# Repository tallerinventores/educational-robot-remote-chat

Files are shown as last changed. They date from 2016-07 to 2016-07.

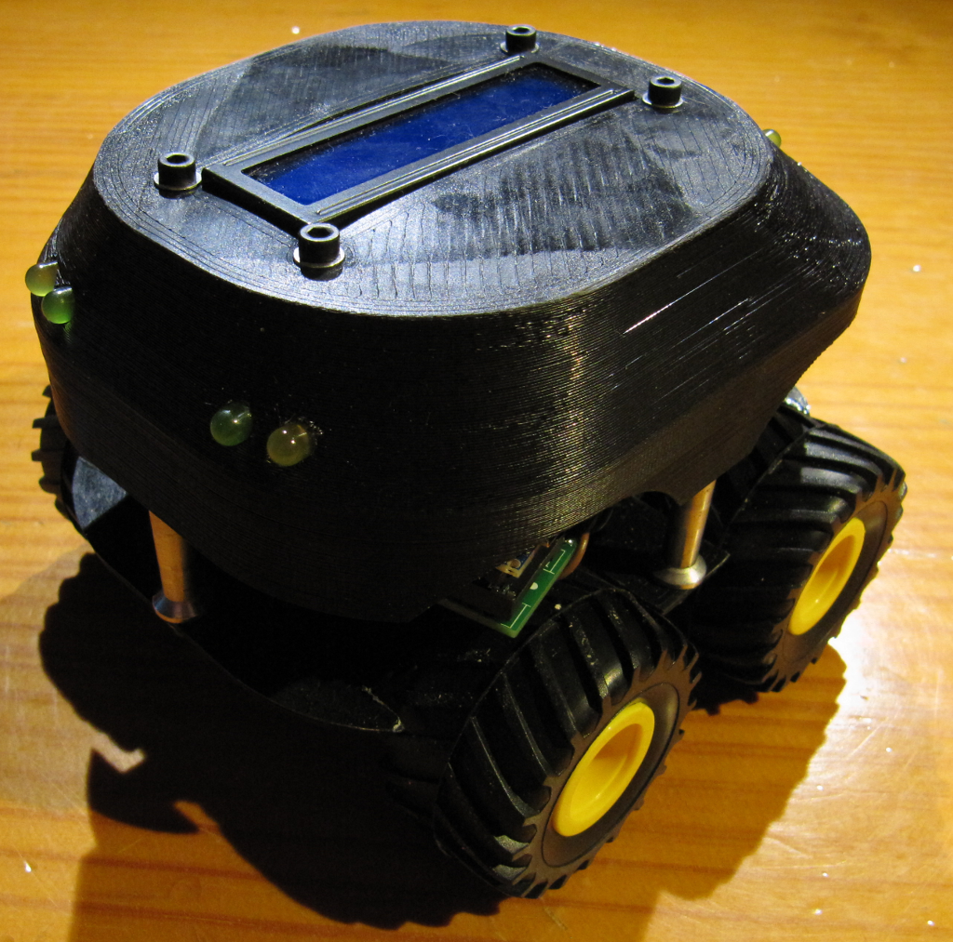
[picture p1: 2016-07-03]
img/photo-errc-2.png

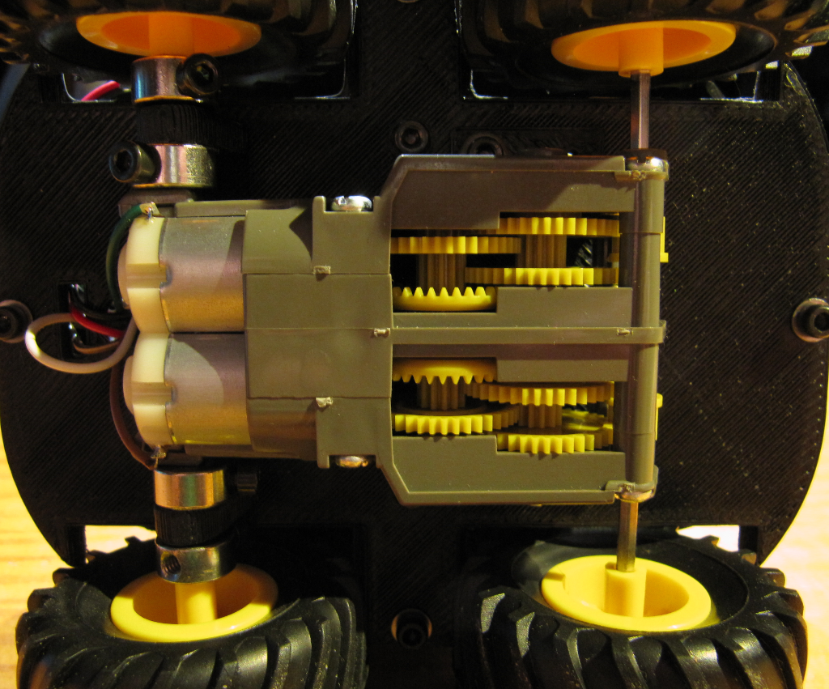
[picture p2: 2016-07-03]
img/photo-errc-5.png

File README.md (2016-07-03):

# educational-robot-remote-chat #

> RC robot w/ chat capabilies for educational use  

* * *

## Resumen ##

Robot interactivo diseñado por los alumnos de la actividad de robótica [Taller
de Inventores](http://tallerinventores.github.io/). Ha sido desarrollado y
optimizado para impresión 3D y pensando en su bajo coste y facilidad de montaje
y uso.

## Instalación ##

En esta sección se cubre la instalación de software y hardware para el montaje
recomendado, mediante [Arduino](http://www.arduino.cc/).

### Requerimientos de software ###

Para poser usar Arduino (v1.6+) con el código fuente proporcionado, son
necesarias las librerías [NewPing](http://playground.arduino.cc/Code/NewPing) y
[NewLiquidCrystal](https://bitbucket.org/fmalpartida/new-liquidcrystal/downloads).
Para generar los archivos aptos para la impresora 3D desde los archivos `.stl`
será necesario adicionalmente un software para esta función, como puede ser
[Slic3r](http://slic3r.org/).

### Requerimientos de hardware ###

Será necesario para su montaje y uso cuatro pilas tipo AA, una pantalla LCD de
dieciséis por dos con interfaz I2C, un sensor de distancia por ultrasonidos tipo
HC-SR04, seis LED de colores, seis resistencias de 330Ω, una de 2,7kΩ, un
transistor BC547, un conjunto de motor Tamiya Twin-Motor y cuatro ruedas Tamiya
Off-road, una placa Robgednaut Zond con un Arduino Nano o compatible y un módulo
de bluetooth HC05. Adicionalmente harán falta tornillos y arandelas de métrica
tres. Se recomienda un macho de misma métrica.

## Uso ##

Instrucciones de montaje y puesta en marcha.

### Montaje del robot ###

1.  Imprimir una unidad de los archivos `chassis.stl` y `base.stl`. Imprimir
    cuatro unidades de `spacer.stl`. Puede ser necesario repasar las piezas
    impresas con el fin de eliminar rebabas.  
2.  Montar la pantalla LCD sobre la parte superior del robot (_chassis_) usando
    cuatro tornillos de métrica tres por doce con arandela, insertados de la
    parte plástica hacia la pantalla, y asegurados con una tuerca cada uno.  
3.  Montar los LED en sus orificios y fijarlos con plástico termofusible si
    fuera necesario.  
4.  Montar el sensor de distancia en el frontal del chasis.  
5.  Presentar el portapilas sobre la parte interior de la parte inferior del
    robot (_base_) y alinear los agujeros de fijación, usar dos tornillos de
    métrica tres por seis, roscando sobre el la estructura del portapilas.  
6.  Montar el motor en la parte externa de la base, y fijarlo mediante dos
    tornillos de métrica tres por seis sobre la rosca que se realiza en sus
    agujeros correspondientes, de forma que quede alineado el eje motriz con el
    centro del hueco de las ruedas.  
7.  Realizar la gestión de cables del motor y del sensor de distancia para que
    entren al cuerpo del robot a través del agujero destinado a ello.  
8.  Montar las ruedas traseras en los ejes del motor.  
9.  Posicionar los ejes delanteros en los agujeros de la base, y montar un
    anillo de retención a cada extremo con tornillos de métrica tres por seis.
    Colocar las ruedas delanteras.  
10. Realizar todas las uniones eléctricas.  
11. Cerrar el robot con tornillos de métrica tres por treinta con arandela,
    añadiendo un espaciador (_spacer_) en cada tornillo entre ambas partes
    principales del robot. Roscar dichos tornillos sobre la rosca previamente
    hecha en los orificios para este propósito de la mitad superior.

### Conexión eléctrica ###

Este proyecto usa [Robgednaut](http://akornsys-rdi.github.io/robgednaut/) Zond
como placa de conexionado, si no dispones de ella puedes ver su esquema de
conexiones en la página oficial.  

Las alimentaciones para todos los dispositivos las provee la placa de control.
Los cables de señal de la pantalla SDA y SCL están conectados a C y D
respectivamente. Las señales del sensor de distancia por ultrasonidos ECHO y
TRIGGER están conectadas a B y A respectivamente. Cada motor está conectado a un
canal de la salida para motores, respetando su polaridad.  

Los LED del robot llevan una resistencia de 330Ω en el ánodo, todos ellos
conectados entre sí y al pin de alimentación de la pantalla. Los cátodos van al
colector del transistor. El emisor está conectado a la masa de la pantalla, y la
base va conectada al pin del expansor I2C que controla la retroiluminación de la
pantalla LCD a través de una resistencia de 2,7kΩ.  

### Firmware ###

El Arduino deberá tener cargado el firmware de control que se incluye en la
carpeta `src` de este repositorio.  

### Software ###

Con la comunicación bluetooth establecida (elementos emparejados), abrir una
aplicación terminal en el dispositivo de control (por ejemplo cutecom) y 
escribir la frase o comando que se desee enviar, finalizada por el caracter
retorno de carro (`0x13`).  

### Bugs ###

Se han observado los siguientes problemas:  

-   Debido a todo el hardware que va dentro del robot, han sido necesarios
    añadir unos separadores entre el chasis y la base.  
-   El interruptor de encendido/apagado es difícil de accionar al quedar dentro
    de la estructura.  
-   Enviar palabras sueltas que no sean comandos, parecen no funcionar.  
-   El software de control provoca al inicio movimientos extraños.  

## Enlaces externos ##

Este proyecto también está presente en:  

-   [Thingiverse](http://www.thingiverse.com/thing:1656508).  

## Créditos ##

Proyecto realizado por Taller de Inventores 2016, representado por:  

-   kwendenarmo <kwendenarmo@akornsys-rdi.net>  

Alumnos del Centro de Formación Padre Piquer:  

-   G, Ayman El-  
-   S, Rubén  
-   S, Sergio

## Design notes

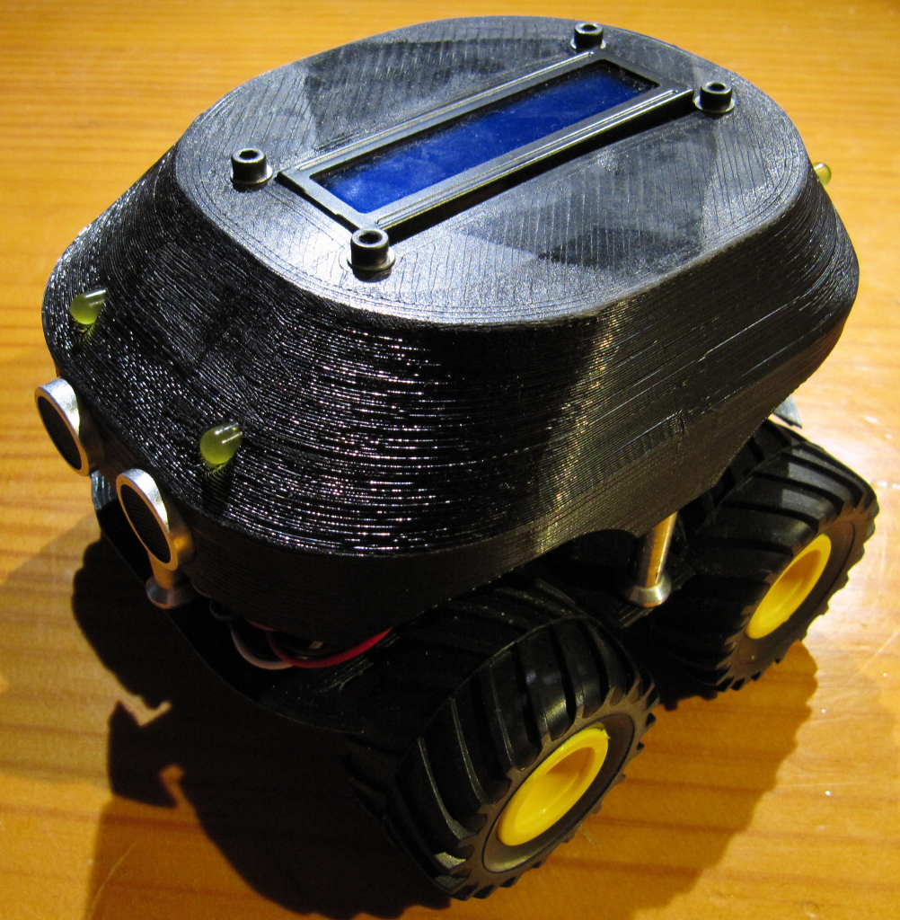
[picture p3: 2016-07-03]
img/photo-errc-1.png

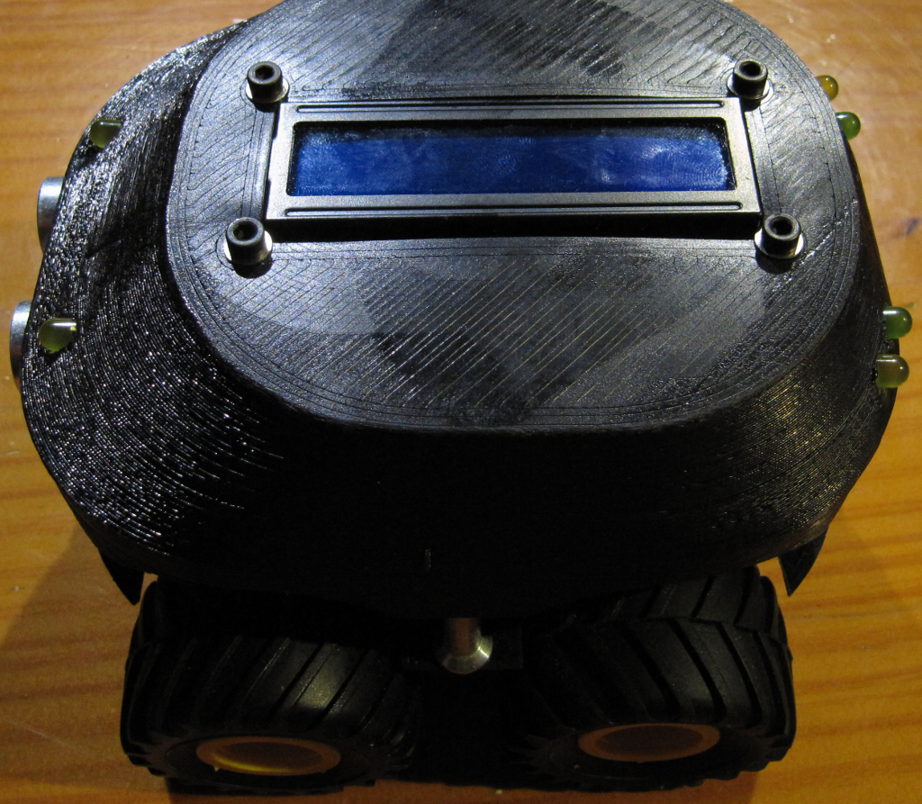
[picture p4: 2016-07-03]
img/photo-errc-6.png

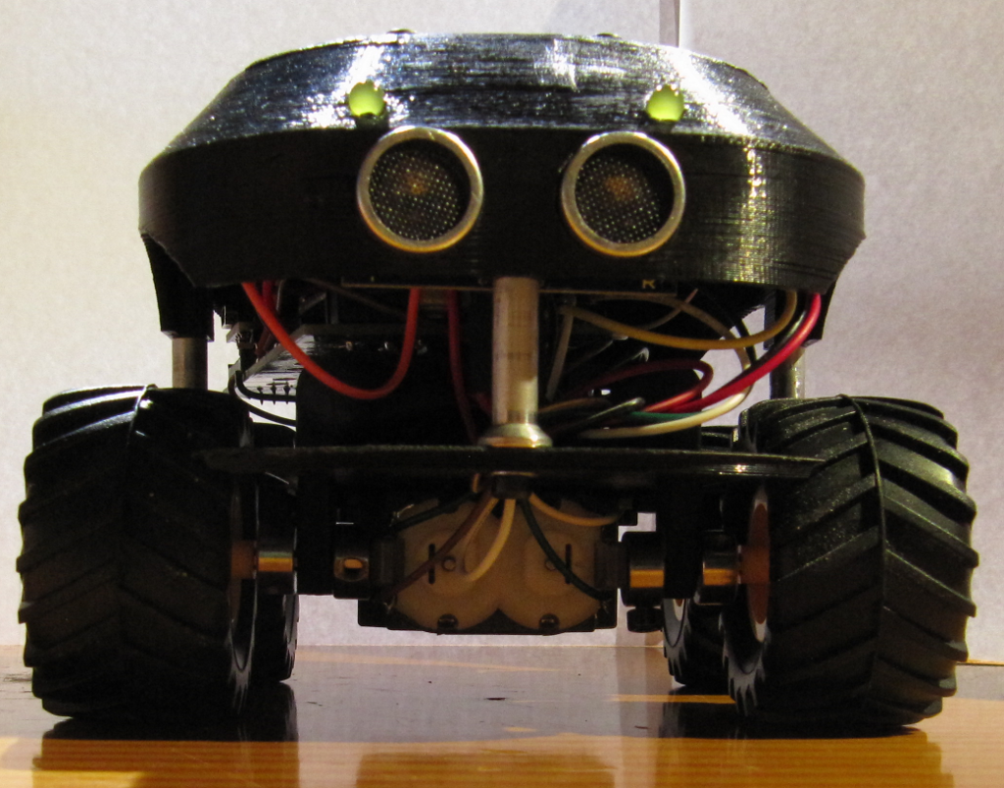
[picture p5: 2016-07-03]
img/photo-errc-8.png

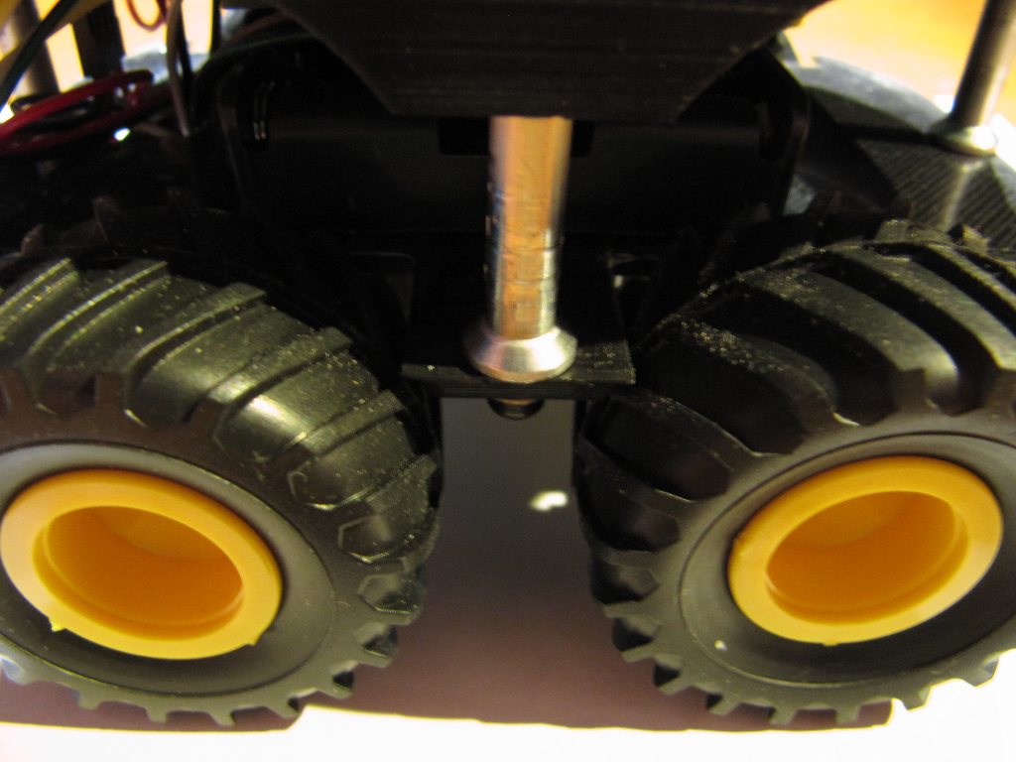
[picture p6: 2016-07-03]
img/photo-errc-7.png

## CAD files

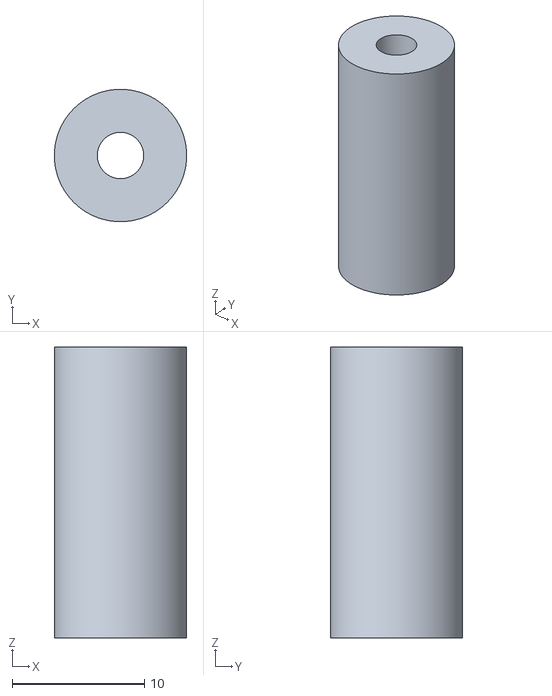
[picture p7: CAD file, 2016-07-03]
3d/spacer.stl
10.0 x 10.0 x 22.0

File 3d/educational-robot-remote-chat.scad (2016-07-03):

/* {{{ %%SECTION_HEADER%%
 * * * *
 * This header information is automatically generated by KodeUtils.
 *
 * File 'educational-robot-remote-chat.scad' edited by kwendenarmo,
 * last modified: 2016-07-03.
 * This file is part of 'educational-robot-remote-chat' package, please see
 * the readme files for more information about this file and this package.
 *
 * Copyright (C) 2016 by kwendenarmo <kwendenarmo@akornsys-rdi.net>
 * Released under the GNU GPLv3
 *
 *    This program is free software: you can redistribute it and/or modify
 *    it under the terms of the GNU General Public License as published by
 *    the Free Software Foundation, either version 3 of the License, or
 *    (at your option) any later version.
 *
 *    This program is distributed in the hope that it will be useful,
 *    but WITHOUT ANY WARRANTY; without even the implied warranty of
 *    MERCHANTABILITY or FITNESS FOR A PARTICULAR PURPOSE.  See the
 *    GNU General Public License for more details.
 *
 *    You should have received a copy of the GNU General Public License
 *    along with this program.  If not, see <http://www.gnu.org/licenses/>.
 *
 * * * *
 * %%EOS_HEADER%% }}}
 */

$fn=360;

/*
 *  Tornillos
 *  -   Portapilas 2x M3x6
 *  -   Motor 2x M3x6
 *  -   Anillos espaciadores 4x M3x6
 *  -   Cierre chasis 4x M3x30 + 1 arandela plana + separador
 *  -   Pantalla 4x M3x12 + 1 arandela plana + 1 tuerca
 */

color("pink") translate([0,0,22]) chasis();
color("pink") translate([-36.5,-27.5,0]) spacer();
color("pink") translate([66.5,-27.5,0]) spacer();
color("pink") translate([15,36.5,0]) spacer();
color("pink") translate([15,-91.25,0]) spacer();
color("pink") translate([0,0,-3]) base();
color("white") translate([-5, -88, 47]) led();
color("white") translate([35, -88, 47]) led();
color("red") translate([-5, 38, 47]) rotate([0,0,180]) led();
color("red") translate([35, 38, 47]) rotate([0,0,180]) led();
color("orange") translate([-13, 36, 47]) rotate([0,0,180]) led();
color("orange") translate([43, 36, 47]) rotate([0,0,180]) led();
translate([33,-60,54.4])  rotate([0,0,90]) lcd();
translate([-7.75,-85,22]) rotate([90,0,0]) hcsr04();
translate([-16,-56.5,0]) portapilas();
translate([-8.75,20,32]) rotate([0,180,180]) roben_zond();
translate([-20,-60,-15.5]) rotate([0,0,-90]) rueda();   //rueda delantera derecha
translate([50,-60,-15.5]) rotate([0,0,90]) rueda();     //rueda delantera izquierda
translate([-20,5,-15.5]) rotate([0,0,-90]) rueda();     //rueda trasera derecha
translate([50,5,-15.5]) rotate([0,0,90]) rueda();       //rueda trasera derecha
translate([15,5,-15.5]) rotate([180,0,0]) motor(1);     //motor
//translate([15,5,-15.5]) rotate([180,0,0]) motor(3);     //motor
translate([15,-60,-15.5]) eje_delantero();              //eje delantero

module chasis() {
    difference() {
        //chasis
        hull() {
            translate([0, -55, 0]) cylinder(r=40, h=20);        //esquina delantera derecha
            translate([30, -55, 0]) cylinder(r=40, h=20);       //esquina delantera izquierda
            translate([0, 0, 0]) cylinder(r=40, h=20);          //esquina trasera derecha
            translate([30, 0, 0]) cylinder(r=40, h=20);         //esquina trasera izquierda
            translate([10, -30, 20]) cylinder(r=40, h=20);      //esquina superior delantera derecha
            translate([20, -30, 20]) cylinder(r=40, h=20);      //esquina superior delantera izquierda
            translate([10, -10, 20]) cylinder(r=40, h=20);     //esquina superior trasera derecha
            translate([20, -10, 20]) cylinder(r=40, h=20);      //esquina superior trasera izquierda
            //translate([0, -15, 10]) cylinder(r=40, h=20);       //lateral derecho
            //translate([30, -15, 10]) cylinder(r=40, h=20);      //lateral izquierdo
        }
        union () {
            //interior chasis
            difference() {
                //silueta chasis
                hull() {
                    translate([0, 0, -1]) cylinder(r=38, h=20);         //esquina trasera derecha
                    translate([0, -55, -1]) cylinder(r=38, h=20);       //esquina delantera derecha
                    translate([30, -55, -1]) cylinder(r=38, h=20);      //esquina delantera izquierda
                    translate([30, 0, -1]) cylinder(r=38, h=20);        //esquina trasera izquierda
                    translate([10, -30, 18]) cylinder(r=38, h=20);      //esquina superior delantera derecha
                    translate([20, -30, 18]) cylinder(r=38, h=20);      //esquina superior delantera izquierda
                    translate([9.5, -10, 18]) cylinder(r=38, h=20);     //esquina superior trasera derecha
                    translate([20, -10, 18]) cylinder(r=38, h=20);      //esquina superior trasera izquierda
                    *translate([30, -15, 10]) cylinder(r=38, h=20);     //esquina superior izquierda
                    *translate([0, -15, 10]) cylinder(r=38, h=20);      //esquina superior derecha
                }
                union() {
                    //topes pantalla
                    union() {
                        translate([31,-25,33.5]) cube([2,10,4.5]);
                        translate([-3,-10,33.5]) cube([2,10,4.5]);
                        translate([13,-60,33.5]) cube([10,2,4.5]);
                    }
                    //topes LED
                    union() {
                        translate([-5, -83, 25]) rotate([90, 0, 0]) cylinder(r=3.5, h=9);  //delantero derecho
                        translate([35, -83, 25]) rotate([90, 0, 0]) cylinder(r=3.5, h=9);  //delantero izquierdo
                        translate([-5, 39, 25]) rotate([90, 0, 0]) cylinder(r=3.5, h=6);   //trasero derecho centro
                        translate([-13, 37, 25]) rotate([90, 0, 0]) cylinder(r=3.5, h=6);  //trasero derecho extremo
                        translate([35, 39, 25]) rotate([90, 0, 0]) cylinder(r=3.5, h=6);   //trasero izquierdo centro
                        translate([43, 37, 25]) rotate([90, 0, 0]) cylinder(r=3.5, h=6);   //trasero izquierdo extremo
                    }
                    //montaje
                    union() {
                        translate([-38,-32.5,0]) cube([5,10,40]);
                        translate([63,-32.5,0]) cube([5,10,40]);
                        translate([5,33,0]) cube([20,5,40]);
                        translate([11.5,-93,0]) cube([7,5,40]);
                    }
                }
            }
            //pantalla LCD
            translate([-3, -60, 37]) color([0,0,0]) {
                union() {
                    translate([5.85, 3.9, 0]) cube([27.3, 72.2, 4]);
                    translate([2.5, 2.5, 0]) cylinder(r=1.75, h=4);
                    translate([2.5, 77.5, 0]) cylinder(r=1.75, h=4);
                    translate([33.5, 2.5, 0]) cylinder(r=1.75, h=4);
                    translate([33.5, 77.5, 0]) cylinder(r=1.75, h=4);
                }
            }
            // LED
            union() {
                translate([-5, -75, 25]) rotate([90, 0, 0]) cylinder(r=2.5, h=20);  //delantero derecho
                translate([-5, -63, 25]) rotate([90, 0, 0]) cylinder(r=3, h=20);    //rebaje delantero derecho
                translate([35, -75, 25]) rotate([90, 0, 0]) cylinder(r=2.5, h=20);  //delantero izquierdo
                translate([35, -63, 25]) rotate([90, 0, 0]) cylinder(r=3, h=20);    //rebaje delantero izquierdo
                translate([-5, 40, 25]) rotate([90, 0, 0]) cylinder(r=2.5, h=10);   //trasero derecho centro
                translate([-5, 33, 25]) rotate([90, 0, 0]) cylinder(r=3, h=10);     //rebaje trasero derecho centro
                translate([-13, 40, 25]) rotate([90, 0, 0]) cylinder(r=2.5, h=10);  //trasero derecho extremo
                translate([-13, 31, 25]) rotate([90, 0, 0]) cylinder(r=3, h=10);    //rebaje trasero derecho extremo
                translate([35, 40, 25]) rotate([90, 0, 0]) cylinder(r=2.5, h=10);   //trasero izquierdo centro
                translate([35, 33, 25]) rotate([90, 0, 0]) cylinder(r=3, h=10);   //rebaje trasero izquierdo centro
                translate([43, 40, 25]) rotate([90, 0, 0]) cylinder(r=2.5, h=10);   //trasero izquierdo extremo
                translate([43, 31, 25]) rotate([90, 0, 0]) cylinder(r=3, h=10);   //rebaje trasero izquierdo extremo
            }
            //ruedas
            union() {
                translate([-50, 5, -15.5]) rotate([0, 90, 0]) cylinder(r=27.5, h=130);      //ruedas traseras
                translate([-50, -60, -15.5]) rotate([0, 90, 0]) cylinder(r=27.5, h=130);    //ruedas delantera
            }
            //sensor ultrasonidos
            translate([0, -90, 0]) union(){
                translate([27.95, 0, 10.6]) rotate([90, 0, 0]) cylinder(r=8.25, h=10);
                translate([1.95, 0, 10.6]) rotate([90, 0, 0]) cylinder(r=8.25, h=10);
                translate([10.5,-0.5,15]) hull() {
                    cube([9,1,5]);
                    translate([0,4,-4]) cube([9,1,11]);
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

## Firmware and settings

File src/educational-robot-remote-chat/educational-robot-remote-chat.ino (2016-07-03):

#include <Wire.h>
#include <LiquidCrystal_I2C.h>
LiquidCrystal_I2C lcd(0x27, 2, 1, 0, 4, 5, 6, 7, 3, POSITIVE);
#include <NewPing.h>
NewPing sonar(2, 3, 200);

//movimiento
#define HALT 0
#define FORWARD 1
#define BACKWARD 2
#define TURN_LEFT 3
#define TURN_RIGHT 4
#define LEFT 1
#define RIGHT 2
#define BOTH 3
//estados
#define STG_WAITING 0
#define STG_HEADER_OK 1
#define STG_LINE_OK 2
//tipos
#define LN_UNKNOWN 0
#define LN_TEXT 1
#define LN_ORDER 2
#define LN_ORDER_NCK 3
#define LN_DONE 4
//cabecera
#define HD_ORDER "ORDEN:"
//usuario
#define USER_NAME "Remote"
#define SAYS " dice:"
#define USERNAME_SAYS USER_NAME SAYS
//ordenes
#define ORD_STOP 0
#define ORD_FORWARD 1
#define ORD_BACKWARD 2
#define ORD_TURN_LEFT 3
#define ORD_TURN_RIGHT 4
#define ORD_CLAXON 5
#define ORD_LIGHT_ON 6
#define ORD_LIGHT_OFF 7
#define ORD_RD_DIST 8
#define TXT_STOP "STOP"
#define TXT_FORWARD "AVANZA"
#define TXT_BACKWARD "RETROCEDE"
#define TXT_LEFT "IZQUIERDA"
#define TXT_RIGHT "DERECHA"
#define TXT_CLAXON "CLAXON"
#define TXT_LON "ENCIENDE"
#define TXT_LOFF "APAGA"
#define TXT_DIST "DISTANCIA"

void setup() {
    //LED
    pinMode(12, OUTPUT);
    pinMode(A0, OUTPUT);
    pinMode(A1, OUTPUT);
    //piezo
    pinMode(4, OUTPUT);
    noTone(4);
    //motores
    pinMode(8, OUTPUT);
    pinMode(7, OUTPUT);
    pinMode(10, OUTPUT);
    pinMode(5, OUTPUT);
    pinMode(9, OUTPUT);
    pinMode(6, OUTPUT);
    moveRobot(HALT, BOTH, 0, 0);
    digitalWrite(7, HIGH);
    digitalWrite(8, HIGH);
    //pantalla
    pinMode(11, INPUT);
    pinMode(13, INPUT);
    lcd.begin(16,2);
    lcd.clear();
    lcd.setBacklight(HIGH);
    lcd.setCursor(0,0);
    lcd.print("Esperando...");
    //comunicación serie
    Serial.begin(9600);
    while(!Serial.available()) {
        digitalWrite(12, HIGH);
        digitalWrite(A0, HIGH);
        digitalWrite(A1, HIGH);
        delay(50);
        digitalWrite(12, LOW);
        digitalWrite(A0, LOW);
        digitalWrite(A1, LOW);
        delay(50);
    }
    while(Serial.available()) Serial.read();
    Serial.flush();
    lcd.clear();
    //lcd.setBacklight(LOW);
}

void loop() {
    char c = 0;
    static unsigned char stage = 0; //0 esperar cabecera; 1 cabecera recibida; 2 final de texto
    static unsigned char pos = 0;
    static unsigned char kind = 0; //0 desconocido; 1 texto; 2 orden
    static String header;
    static String received;

    if (Serial.available()) {
        c = Serial.read();
        if (isAscii(c)) {
            //identificación de fin de línea `CR`
            if (c == 13) {
                stage = STG_LINE_OK;
                received.trim();
                printIncoming(received, kind);
                if (kind == LN_ORDER) parseOrder(received);
                header = "";
                received = "";
                stage = STG_WAITING;
                kind = LN_UNKNOWN;
                pos = 0;
            }
            //identificación de cabecera
            else if ((c == ' ') && (pos > 0) && (kind == LN_UNKNOWN) && (stage == STG_WAITING)) {
                header.toUpperCase();
                header.trim();
                if (header == HD_ORDER) {
                    kind = LN_ORDER;
                    received.trim();
                    received = received.substring(header.length());
                }
                else {
                    kind = LN_TEXT;
                    received += c;
                }
                stage = STG_HEADER_OK;
            }
            else {
                if (isAlphaNumeric(c) || isPunct(c)) {
                    pos++;
                }
                received += c; //caracteres payload
                if (kind == LN_UNKNOWN) header += c; //caracteres de cabecera
            }
        }
    }
}

void moveRobot(unsigned char course, unsigned char motor, unsigned char value, unsigned int distance) {
    switch (motor) {
      case LEFT:
        if (course == HALT) {
            digitalWrite(5, LOW);
            digitalWrite(10, LOW);
        }
        else if (course == FORWARD) {
            digitalWrite(10, LOW);
            analogWrite(5, value);
            delay(distance);
            digitalWrite(5, LOW);
        }
        else if (course == BACKWARD) {
            digitalWrite(5, LOW);
            analogWrite(10, value);
            delay(distance);
            digitalWrite(10, LOW);
        }
        break;
      case RIGHT:
        if (course == HALT) {
            digitalWrite(6, LOW);
            digitalWrite(9, LOW);
        }
        else if (course == FORWARD) {
            digitalWrite(6, LOW);
            analogWrite(9, value);
            delay(distance);
            digitalWrite(9, LOW);
        }
        else if (course == BACKWARD) {
            digitalWrite(9, LOW);
            analogWrite(6, value);
            delay(distance);
            digitalWrite(6, LOW);
        }
        break;
      case BOTH:
        if (course == HALT) {
            digitalWrite(5, LOW);
            digitalWrite(10, LOW);
            digitalWrite(6, LOW);
            digitalWrite(9, LOW);
        }
        else if (course == FORWARD) {
            digitalWrite(10, LOW);
            analogWrite(5, value);
            digitalWrite(6, LOW);
            analogWrite(9, value);
            delay(distance);
            digitalWrite(5, LOW);
            digitalWrite(9, LOW);
        }
        else if (course == BACKWARD) {
            digitalWrite(5, LOW);
            analogWrite(10, value);
            digitalWrite(9, LOW);
            analogWrite(6, value);
            delay(distance);
            digitalWrite(10, LOW);
            digitalWrite(6, LOW);
        }
        else if (course == TURN_LEFT) {
            digitalWrite(5, LOW);
            analogWrite(10, value);
            digitalWrite(6, LOW);
            analogWrite(9, value);
            delay(distance);
            digitalWrite(10, LOW);
            digitalWrite(9, LOW);
        }
        else if (course == TURN_RIGHT) {
            digitalWrite(10, LOW);
            analogWrite(5, value);
            digitalWrite(9, LOW);
            analogWrite(6, value);
            delay(distance);
            digitalWrite(5, LOW);
            digitalWrite(6, LOW);
        }
    }
}

void printIncoming(String str, unsigned char type) {
    String line;
    
    if (type == LN_TEXT) {
        playEvent(LN_TEXT);
        if (str.length() > 16) {
            for (unsigned char i = 0; i < (str.length() - 16); i++) {
                lcd.clear();
                lcd.setCursor(0,0);
                lcd.print(USERNAME_SAYS);
                lcd.setCursor(0,1);
                line = str.substring(0+i,16+i);
                lcd.print(line);
                delay(250);
            }
        }
        else {
            lcd.clear();
            lcd.setCursor(0,0);
            lcd.print(USERNAME_SAYS);
            lcd.setCursor(0,1);
            lcd.print(str);
        }
    }
    else if (type == LN_ORDER) {
        lcd.clear();
        lcd.setCursor(0,0);
        lcd.print("Orden recibida:");
        lcd.setCursor(0,1);
        lcd.print(str);
    }
    else if (type == LN_DONE) {
        lcd.clear();
        lcd.setCursor(0,0);
        lcd.print("Orden realizada:");
        lcd.setCursor(0,1);
        lcd.print(str);
    }
    else if (type == LN_ORDER_NCK) {
        lcd.clear();
        lcd.setCursor(0,0);
        lcd.print("  Error: orden  ");
        lcd.setCursor(0,1);
        lcd.print("  desconocida.  ");
    }
}

void parseOrder(String order) {
    String upperOrder;
    String strDist;

    upperOrder = order;
    upperOrder.toUpperCase();
    if (upperOrder == TXT_STOP) {
        playEvent(LN_ORDER);
        moveRobot(HALT, BOTH, 0, 0);
        printIncoming(order, LN_DONE);
        playEvent(LN_DONE);
    }
    else if (upperOrder == TXT_FORWARD) {
        playEvent(LN_ORDER);
        moveRobot(FORWARD, BOTH, 255, 1000);
        printIncoming(order, LN_DONE);
        playEvent(LN_DONE);
    }
    else if (upperOrder == TXT_BACKWARD) {
        playEvent(LN_ORDER);
        moveRobot(BACKWARD, BOTH, 255, 1000);
        printIncoming(order, LN_DONE);
        playEvent(LN_DONE);
    }
    else if (upperOrder == TXT_LEFT) {
        playEvent(LN_ORDER);
        moveRobot(TURN_LEFT, BOTH, 255, 1000);
        printIncoming(order, LN_DONE);
        playEvent(LN_DONE);
    }
    else if (upperOrder == TXT_RIGHT) {
        playEvent(LN_ORDER);
        moveRobot(TURN_RIGHT, BOTH, 255, 1000);
        printIncoming(order, LN_DONE);
        playEvent(LN_DONE);
    }
    else if (upperOrder == TXT_CLAXON) {
        playEvent(LN_ORDER);
        delay(250);
        playEvent(ORD_CLAXON);
        printIncoming(order, LN_DONE);
        playEvent(LN_DONE);
    }
    else if (upperOrder == TXT_LON) {
        playEvent(LN_ORDER);
        delay(250);
        lcd.setBacklight(HIGH);
        printIncoming(order, LN_DONE);
        playEvent(LN_DONE);
    }
    else if (upperOrder == TXT_LOFF) {
        playEvent(LN_ORDER);
        delay(250);
        lcd.setBacklight(LOW);
        printIncoming(order, LN_DONE);
        playEvent(LN_DONE);
    }
    else if (upperOrder == TXT_DIST) {
        playEvent(LN_ORDER);
        delay(250);
        strDist = (String)sonar.ping_cm();
        printIncoming(order + " " + strDist, LN_DONE);
        playEvent(LN_DONE);
    }
    else {
        printIncoming(order, LN_ORDER_NCK);
        playEvent(LN_ORDER_NCK);
    }
}

void playEvent(unsigned char type) {
    switch (type) {
      case LN_TEXT:
        tone(4, 880, 100);
        delay(100);
        tone(4, 1760, 100);
        delay(100);
        break;
      case LN_ORDER:
        tone(4, 440, 100);
        delay(100);
        break;
      case LN_ORDER_NCK:
        tone(4, 440, 50);
        delay(75);
        tone(4, 440, 50);
        delay(75);
        tone(4, 440, 50);
        delay(50);
        break;
      case LN_DONE:
        tone(4, 440, 100);
        delay(150);
        tone(4, 440, 100);
        delay(100);
        break;
      case ORD_CLAXON:
        tone(4, 2000, 500);
        delay(1000);
        break;
    }
    noTone(4);
}
